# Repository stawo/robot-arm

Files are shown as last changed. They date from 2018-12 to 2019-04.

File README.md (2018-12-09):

This is a small project aimed at building a 6 DOF robot arm using inexpensive components, and control it through a Raspberry Pi.

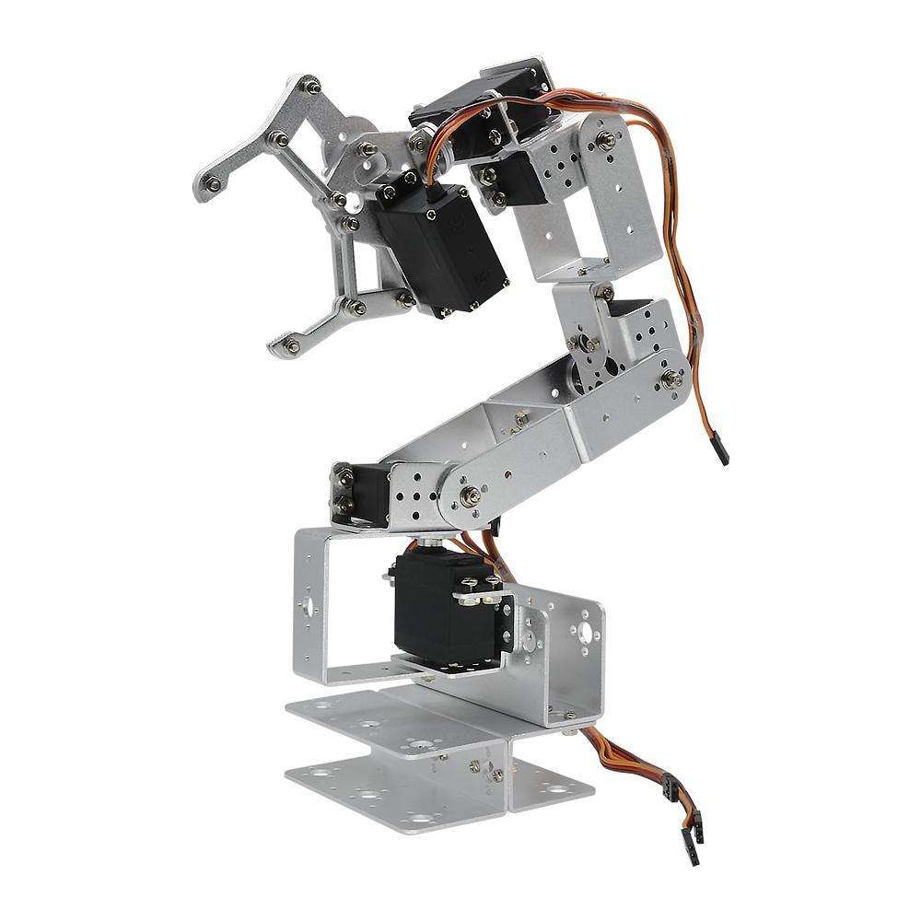
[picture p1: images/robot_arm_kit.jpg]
robot arm kit Robot Arm Kit


# Table of Contents
- [Table of Contents](#table-of-contents)
- [BOM](#bom)
- [Some Theory](#some-theory)
  - [Controlling Servo Motors](#controlling-servo-motors)
  - [Servo motor feedback](#servo-motor-feedback)
- [Raspberry Pi configuration](#raspberry-pi-configuration)
  - [Raspberry Pi set up](#raspberry-pi-set-up)
  - [Controlling servo motors with Raspberry Pi and the PWM Driver PCA9685](#controlling-servo-motors-with-raspberry-pi-and-the-pwm-driver-pca9685)
  - [Reading the feedback from servo motors with Raspberry Pi](#reading-the-feedback-from-servo-motors-with-raspberry-pi)

# BOM
List of components used:
* Raspberry Pi 2 Model B
* 32GB Micro SD card
* Robot Arm mechanical kit (Diymore ROT3U 6DOF Aluminium Robot Arm Mechanical Clamp Claw Kit, https://www.amazon.de/gp/product/B01LY4RHX2/)
* 6x Servo Motors (Lewan Soul LD-27MG, http://www.lewansoul.com/product/detail-19.html)
* 12V 30A Switching Power Supply (Xktts Ueercrr 12V 30A 360W, https://www.amazon.de/gp/product/B00P2CTT26)
* DC/DC 4.5-30V to 1-30V 12A Buck Converter (https://www.amazon.de/gp/product/B00HV4EPG8)
* Dual USB DC/DC Step Down Converter (https://www.amazon.de/gp/product/B0768D2NYH)
* Sunfounder PCA9685 16 Channel 12 Bit PMW Servo Driver (http://wiki.sunfounder.cc/index.php?title=PCA9685_16_Channel_12_Bit_PWM_Servo_Driver)
* 4x 45 cm Servo Extension Cable (https://www.amazon.de/gp/product/B01M7N77XC)
* 4x 20cm female-female Dupont jumper wire cable (https://www.amazon.de/gp/product/B00OL6JZ3C)
* 3-cores electric wire with plug
* 2-cores wire
* screws/nails
* USB-Micro USB cable

Tools:
* Multimeter
* Electric screwdriver
* Monitor/Keyboard/Mouse/Wi-Fi adapter/SD Adapter for Micro SD for the Raspberry Pi

Just to give a reference, I personally ordered almost everything on Amazon for the sake of simplicity (or laziness), and spent around 200€.

|**NOTE**|
|--------|
|The servo motors have to be physically modified in order to read the internal potentiometer.|

# Some Theory
Before moving on, it is necessary to understand how the various elements work, especially parts like servo motors, in order to avoid problems (i.e., avoid burning stuff like me due to too much excitement and not knowing how things work!).

## Controlling Servo Motors
A servo motor is usually controllable through PWM (Pulse Width Modulation). Specifically, its arm position depends on the width (or length) of the pulse applied to it.
A PWM signal encodes a ratio. The ratio of on to off is needed to get all the information; on alone is not enough. 
As a concrete example, PWM might be running at a frequency of 200Hz (or a period of 5ms). A 50% of maximum power signal (also known as Duty Cycle) would be on for 2.5ms, and off for 2.5ms. 
Change the frequency to 1000Hz, and hence the period becomes 1ms. The 50% duty cycle would now be 0.5ms on, and 0.5ms off. That PWM signal still encodes the same 50% power information.

Usually, servos can rotate between 0 and 180°. So we have to adjust the pulse length in between. A length of 1.5ms (7.5% duty cycle) thus gives an angle of 90°. And all at precisely 50 times per second (50Hz).
This diagram summarizes how a servo motor is controlled through PWM:

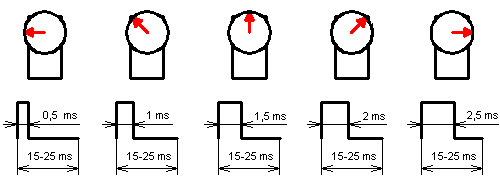
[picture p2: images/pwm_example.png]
pwm example PWM Example


In my case I use the Lewan Soul LD-27MG, which has the following specs:
* working voltage: 6-7.4 V
* min working current: 1 A
* angle: between 0° and 270°
* Pulse Period: 20ms
  thus Frequency: 50Hz
* Pulse Width Range: between 0.5ms and 2.5ms
  thus Duty Cycle: between 2.5% and 12.5%

Conversion table:
Angle   | Pulse Width (ms) | Duty Cycle (%)
------- | ---------------- | --------------
0°      | 0.5              | 2.5
45°     | 0.8333           | 4.1666
90°     | 1.1666           | 5.8333
135°    | 1.5              | 7.5
180°    | 1.8333           | 9.1666
225°    | 2.1666           | 10.8333
270°    | 2.5              | 12.5

Links:
* https://www.teachmemicro.com/raspberry-pi-pwm-servo-tutorial/
* https://tutorials-raspberrypi.com/raspberry-pi-servo-motor-control/

## Servo motor feedback
Normal servo motors do not provide a feedback to the control board (in our case, the Raspberry Pi).
They simply take the PWM generated and do their best to fulfill the "request".

For our robot arm this is not ideal, because the arm could get stuck while doing a movement (for example, we try to push the arm against the table), and this leads to a stall of the servo motor.
Stalling a servo motor will damage it and the control board, as it will increase the current load (see https://electronics.stackexchange.com/questions/274721/how-does-blocking-a-servo-dc-motor-break-it).

Especially in my setup, once the PCA9685 control board sends the PWM signal to the servo motor, there is no way to stop the PWM signal or turn off the servo, and the board will burn out (it happened to me) if the servo stalls.

To understand if a servo motor is in stall (or, alternatively, is operating correctly), we need a feedback from it.
We can achieve this by tapping the potentiometer inside the servo motor, and read the measured voltage.

**[TO DO: How to modify the servo motors]**

Links:
* https://www.youtube.com/watch?v=w7qRs6tvxlM
* https://learn.adafruit.com/analog-feedback-servos/using-feedback
* https://electronics.stackexchange.com/questions/214761/how-to-measure-servo-potentiometer

# Raspberry Pi configuration

I'm running the Raspberry Pi using Raspbian Stretch with desktop (https://www.raspberrypi.org/downloads/raspbian/).

Here is the Raspberry Pi GPIO layout (http://pi4j.com/pins/model-2b-rev1.html) for reference:
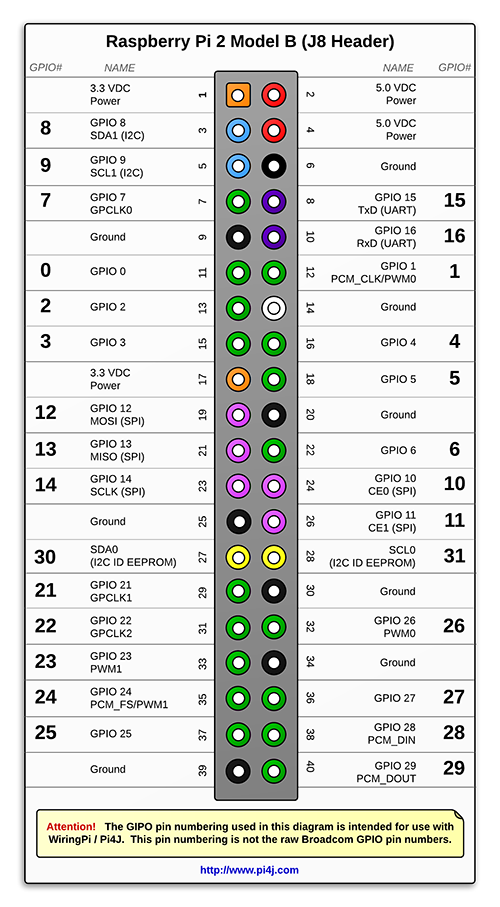
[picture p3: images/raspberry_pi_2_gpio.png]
raspberry pi gpio Raspberry Pi 2 GPIO


## Raspberry Pi set up
To be able to control servo motor through the PCA9685 controller, we need to perform the following steps:
1. Activate the I2C interface in the Raspberry
    * run the command
    ``sudo raspi-config``
    * go to “Interfaces”, select “I2C”, select “Yes”
2. Configuring Raspberry Pi for I2C.
    * Install the following packages:
    ``sudo apt-get install python-smbus``
    ``sudo apt-get install i2c-tools``
    * Add the following lines to ``/etc/modules``:
    ``i2c-dev``
    ``i2c-bcm2708``
    * Reboot the Pi
3. Check that the PCA9685 controller is properly connected and it's set to its default address:
  ``sudo i2cdetect -y 1``
  It should show up at 0x40 (binary 1000000) as follows:
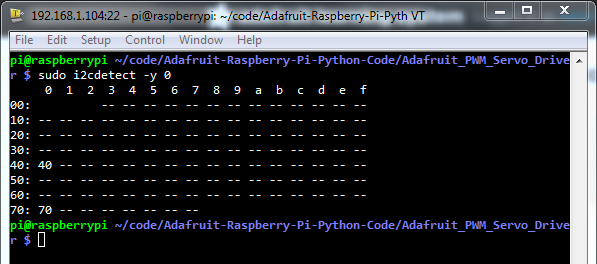
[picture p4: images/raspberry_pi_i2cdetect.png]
raspberry pi i2cdetect i2cdetect
  
4. Connect the PCA9685 controller as in the diagram
5. [optional] Create/activate the Python environment of your choice
6. Install the library https://github.com/adafruit/Adafruit_Python_PCA9685 by running the command:
  ``sudo pip install adafruit-pca9685``

Links:
* https://learn.adafruit.com/adafruit-16-channel-servo-driver-with-raspberry-pi/configuring-your-pi-for-i2c

## Controlling servo motors with Raspberry Pi and the PWM Driver PCA9685
**[TO DO]**

## Reading the feedback from servo motors with Raspberry Pi
**[TO DO]**

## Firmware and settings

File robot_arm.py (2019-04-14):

# ----------------------------
# LIBRARIES

# External libraries
import time
# Import the PCA9685 module.
import Adafruit_PCA9685
import board
import busio
import adafruit_ads1x15.ads1115 as ADS
from adafruit_ads1x15.analog_in import AnalogIn
import pandas

# Uncomment to enable debug output.
#import logging
#logging.basicConfig(level=logging.DEBUG)

# ----------------------------
# PARAMETERS

# ----------------------------
# CODE

class Servo:

    # PARAMETERS
    SERVO_MOTOR_DUTY_CYCLE_MIN = 2.5  # Min duty cycle, in %
    SERVO_MOTOR_DUTY_CYCLE_MAX = 12.5  # Max duty cycle, in %
    SERVO_MOTOR_ANGLE_MIN = 0  # Min angle, in degrees
    SERVO_MOTOR_ANGLE_MAX = 270  # Max angle, in degrees
    
    # Angle to cover at each step of the calibration
    # We define it so we can have clear ads values between each step,
    # as the ads readings fluctuate, and too close angles will not be
    # easily distinguishable.
    SERVO_MOTOR_ANGLE_CALIBRATION_STEP = 10

    # We define how many seconds the feedback loop will
    # wait while the servo tries to reach the designated angle
    # before intervening if no movement is detected.
    # This is needed in those situations where the servo is
    # blocked but keeps trying to reach the desired angle.
    MAX_TIME_BEFORE_EMERGENCY_STOP = 1

    # Value for the alpha parameter in the calculation of
    # the exponential moving average (ema)
    # https://en.wikipedia.org/wiki/Moving_average#Exponential_moving_average
    CALIBRATION_EMA_ALPHA = 0.8
    # Percentage that says when the ema converged to a
    # value that can be considered stable
    CALIBRATION_EMA_CONVERGENCE_PERCENTAGE = 0.001
    # CALIBRATION_EMA_CONVERGENCE_ABSOLUTE = 0.001

    def __init__(
        self
        , pwm_board
        , pwm_board_servo_channel
        , pwm_board_resolution
        , angle_min
        , angle_max
        , ads_board
        , ads_board_channel
        , angle_ads_value_map):
        
        if not isinstance(pwm_board, Adafruit_PCA9685.PCA9685):
            raise ValueError('The pwm_board parameter must be a Adafruit_PCA9685.PCA9685 instance.')
        
        if not isinstance(pwm_board_servo_channel, int) and pwm_board_servo_channel >= 0:
            raise ValueError('The pwm_board_servo_channel parameter must be a positive integer >= 0.')
        
        if not isinstance(pwm_board_resolution, int) and pwm_board_resolution > 0:
            raise ValueError('The pwm_board_resolution parameter must be a positive integer > 0.')
        
        if not isinstance(ads_board, ADS.ADS1115):
            raise ValueError('The ads_board parameter must be a ADS.ADS1115 instance.')
        
        if not isinstance(ads_board_channel, int) and ads_board_channel >= 0:
            raise ValueError('The ads_board_channel parameter must be a positive integer >= 0.')
        
        self.PWM_BOARD = pwm_board
        self.PWM_BOARD_SERVO_CHANNEL = pwm_board_servo_channel
        self.PWM_BOARD_RESOLUTION = pwm_board_resolution
        self.ADS_BOARD = ads_board
        self.ADS_BOARD_CHANNEL = ads_board_channel
        
        # If the Servo motor doesn't have a valid angle_ads_value_map
        # we do not allow it to move
        self.BLOCKED = True

        self.__ads_chan = AnalogIn(self.ADS_BOARD, self.ADS_BOARD_CHANNEL)

        if isinstance(angle_ads_value_map, pandas.DataFrame) \
            and angle_ads_value_map.columns.values.tolist() == ['angle','ads_value']:
            self.BLOCKED = False
            self.ANGLE_ADS_VALUE_MAP = angle_ads_value_map

            # Try to evaluate the current position of the servo
            self.current_angle = self.__evaluate_current_angle()
    
    def __evaluate_current_angle(self):
        """
        Function to evaluate the current angle based on the ads value.

        To evaluate the current angle of the servo we:
        * read the current ads value
        * use the angle_ads_value_map to estimate the angle

        Returns
		-------
            int
            The estimated angle of the servo.

        """

        current_ads_value = self.__ads_chan.value
        closest_angle = self.ANGLE_ADS_VALUE_MAP.ix[(self.ANGLE_ADS_VALUE_MAP.ads_value-current_ads_value).abs().argsort()[:1]].angle.values[0]
        
        return closest_angle
        
    def __convert_angle_to_pwm_board_step(self, angle):
        '''
        Transform a given angle to the proper step for the PWB board.
        Usually boards like the PCA9685 uses a discrete representation for the PWM.
        They divide the Pulse Cycle in 4096 steps, and we have to say from
        which step to which step we want the pulse to be high.

        We assume that, for servo motors, the first step is 0,
        so we just have to calculate the ending step, so to represent the given angle
        as a discrete PWM.

        To calculate the step, we first calculate the relative duty cycle of the angle.
        We then multiply the PWM_BOARD_RESOLUTION by the duty cycle (which is a percentage).
        '''
        
        # Round the angle to the closest valid one w.r.t. SERVO_MOTOR_ANGLE_CALIBRATION_STEP
        angle = int(angle) - int(angle)%self.SERVO_MOTOR_ANGLE_CALIBRATION_STEP
         
        # Check that the angle is within the limits
        if (angle < self.SERVO_MOTOR_ANGLE_MIN) | (angle > self.SERVO_MOTOR_ANGLE_MAX):
            raise ValueError('The given angle ({}) is outside the limits!'.format(angle))

        # We make sure angle is treated as a float
        servo_duty_cycle = float(angle)/(self.SERVO_MOTOR_ANGLE_MAX-self.SERVO_MOTOR_ANGLE_MIN)*(self.SERVO_MOTOR_DUTY_CYCLE_MAX-self.SERVO_MOTOR_DUTY_CYCLE_MIN) + self.SERVO_MOTOR_DUTY_CYCLE_MIN

        # Check that the duty cycle is within the limits
        # This check is just to be sure that also the angle parameters are set correctly
        if (servo_duty_cycle < self.SERVO_MOTOR_DUTY_CYCLE_MIN) | (servo_duty_cycle > self.SERVO_MOTOR_DUTY_CYCLE_MAX):
            raise ValueError('The given servo duty cycle ({}) is outside the limits!'.format(servo_duty_cycle))

        # The step must be an integer, as the board does not accept floats
        pwm_step = int(self.PWM_BOARD_RESOLUTION*servo_duty_cycle/100)

        # print('angle: {}\tservo_duty_cycle: {}\tpwm_step: {}'.format(angle,servo_duty_cycle,pwm_step))

        return pwm_step

    def __move(self, angle, raise_if_out_of_range = False):
        '''
        Function that moves the specified servo to the given angle.
        It has no feedback control!

        We use this function as the low-level instruction to move
        the servo used by other functions of the class if needed.
        '''

        if raise_if_out_of_range:
            if angle < self.SERVO_MOTOR_ANGLE_MIN: raise ValueError('The given angle ({}) is outside the limits!'.format(angle))
            if angle > self.SERVO_MOTOR_ANGLE_MAX: raise ValueError('The given angle ({}) is outside the limits!'.format(angle))
        else:
            # If the specified angle is out of range, we block it to the closest limit
            if angle < self.SERVO_MOTOR_ANGLE_MIN: angle = self.SERVO_MOTOR_ANGLE_MIN
            if angle > self.SERVO_MOTOR_ANGLE_MAX: angle = self.SERVO_MOTOR_ANGLE_MAX
        
        pwm_step = self.__convert_angle_to_pwm_board_step(angle)
        self.PWM_BOARD.set_pwm(self.PWM_BOARD_SERVO_CHANNEL, 0, pwm_step)

    def calibrate(self, calibration_map_path):
        
        print('CALIBRATION OF THE SERVO MOTOR')
        print('This function will move the servo motor from {} (SERVO_MOTOR_ANGLE_MIN) to {} (SERVO_MOTOR_ANGLE_MAX),'.format(self.SERVO_MOTOR_ANGLE_MIN,self.SERVO_MOTOR_ANGLE_MAX))
        print('and register the output value of the ADS board.')
        print()
        print('MAKE SURE THE SERVO IS FREE TO MOVE!')
        answer = input("Enter YES to proceed: ")
        if answer.lower() != "yes":
            print("I will not continue the calibration.")
            return

        print('Starting calibration.')

        calibration_map_angle_to_ads_value = []

        # Move to the minimum angle, in case the servo is at another angle
        self.__move(self.SERVO_MOTOR_ANGLE_MIN)

        # Initialize the exponential moving average        
        ema = self.__ads_chan.value
        
        TIME_STEP_DURATION = 0.2
        NUM_OF_TIME_STEPS = 10

        # We let the ems to be estimated over some cycles
        # before checking if it converged
        for counter in range(NUM_OF_TIME_STEPS):
            old_ema = ema
            ema = self.CALIBRATION_EMA_ALPHA*self.__ads_chan.value + (1-self.CALIBRATION_EMA_ALPHA)*ema
            
            print('value: {:.2f}\t\tema: {:.2f}\t\tdiff percentage: {:.4f}'.format(self.__ads_chan.value,ema,abs((ema-old_ema)/ema)))
            
            time.sleep(TIME_STEP_DURATION)
        
        while True:
            old_ema = ema
            ema = self.CALIBRATION_EMA_ALPHA*self.__ads_chan.value + (1-self.CALIBRATION_EMA_ALPHA)*ema
            
            print('value: {:.2f}\t\tema: {:.2f}\t\tdiff percentage: {:.4f}'.format(self.__ads_chan.value,ema,abs((ema-old_ema)/ema)))
            
            if abs((ema-old_ema)/ema) <= self.CALIBRATION_EMA_CONVERGENCE_PERCENTAGE: break
            
            time.sleep(TIME_STEP_DURATION)
            
        
        print('Moved to 0.')
        time.sleep(2)

        # Move to the minimum angle, in case the servo is at another angle
        # self.__move(self.SERVO_MOTOR_ANGLE_MIN)
        # print('Moved to 0.')
        # time.sleep(2)
        
        for angle in range(self.SERVO_MOTOR_ANGLE_MIN,self.SERVO_MOTOR_ANGLE_MAX+1, self.SERVO_MOTOR_ANGLE_CALIBRATION_STEP):
            
            self.__move(angle)

            # Initialize the exponential moving average
            ema = self.__ads_chan.value

            # We let the ems to be estimated over some cycles
            # before checking if it converged
            for counter in range(NUM_OF_TIME_STEPS):
                old_ema = ema
                ema = self.CALIBRATION_EMA_ALPHA*self.__ads_chan.value + (1-self.CALIBRATION_EMA_ALPHA)*ema
                
                print('value: {:.2f}\t\tema: {:.2f}\t\tdiff percentage: {:.4f}'.format(self.__ads_chan.value,ema,abs((ema-old_ema)/ema)))
                
                time.sleep(TIME_STEP_DURATION)
            
            while True:
                old_ema = ema
                ema = self.CALIBRATION_EMA_ALPHA*self.__ads_chan.value + (1-self.CALIBRATION_EMA_ALPHA)*ema
                
                print('value: {:.2f}\t\tema: {:.2f}\t\tdiff percentage: {:.4f}'.format(self.__ads_chan.value,ema,abs((ema-old_ema)/ema)))
                
                if abs((ema-old_ema)/ema) <= self.CALIBRATION_EMA_CONVERGENCE_PERCENTAGE: break
                
                time.sleep(TIME_STEP_DURATION)
            
            
            self.current_angle = angle

            # Read voltage and use it to evaluate if the servo is stuck
            calibration_map_angle_to_ads_value.append([angle,self.__ads_chan.value])

            print('Moved to angle {}, ads value is {}'.format(angle,self.__ads_chan.value))
        
        calibration_map_angle_to_ads_value_df = pandas.DataFrame(calibration_map_angle_to_ads_value, columns = ['angle','ads_value'])
        calibration_map_angle_to_ads_value_df.to_csv(calibration_map_path, index=False)

    def move(self, angle):
        '''
        We move the specified servo to the given angle.
        We check the ads value for feedback and use it
        to either continuing the movement or block it.

        The process is as follow:
        - divide the desired angle in steps
        - for each step:
            - move to the current step
            - check every X seconds if the servo actually moved
            by reading the ads value
            - if no movement is detected, try to move back to the
            last step

        '''

        if self.BLOCKED:
            raise ValueError('The Servo motor is blocked. Cannot perform movements!')

        print('Move to angle {}'.format(angle))

        starting_angle = self.current_angle
        versus = 'UP' if angle > starting_angle else 'DOWN'

        for partial_angle in range(starting_angle, angle, self.SERVO_MOTOR_ANGLE_CALIBRATION_STEP):
            
            self.__move(partial_angle)
            
            start_time = time.time()

            while True:
                time.sleep(0.2)
                
                evaluated_angle = self.__evaluate_current_angle()

                if (time.time()-start_time) >= MAX_TIME_BEFORE_EMERGENCY_STOP:
                    
                    if (versus == 'UP' and self.current_angle <= evaluated_angle):
                        pass

            
            self.current_angle = partial_angle

class RobotArm:

    # PARAMETERS
    PWM_BOARD_RESOLUTION = 4096 # PWM control board resolution
    SERVO_MOTOR_FREQUENCY = 50 #In Hz
    
    JOINT_0_ANGLE_ADS_VALUE_MAP_PATH = 'data/angle_ads_value_map_joint_0.csv'

    def __init__(self):
        
        print('Initialize PWM board controller')
        # Initialise the PCA9685 using the default address (0x40).
        self.__pwm = Adafruit_PCA9685.PCA9685()

        print('Set frequency')
        # Set the frequency
        self.__pwm.set_pwm_freq(self.SERVO_MOTOR_FREQUENCY)

        self.__i2c = busio.I2C(board.SCL, board.SDA)
        self.__ads1 = ADS.ADS1115(self.__i2c)
        # self.__ads2 = ADS.ADS1115(i2c)
        
        self.__joints = []
        self.__joints.append(Servo(self.__pwm,0,self.PWM_BOARD_RESOLUTION,0,270,self.__ads1,0, pandas.read_csv(self.JOINT_0_ANGLE_ADS_VALUE_MAP_PATH)))
        # self.__joints.append(Servo(self.__pwm,1,self.PWM_BOARD_RESOLUTION,0,270,self.__ads1,1))
        # self.__joints.append(Servo(self.__pwm,2,self.PWM_BOARD_RESOLUTION,0,270,self.__ads1,2))
        # self.__joints.append(Servo(self.__pwm,3,self.PWM_BOARD_RESOLUTION,0,270,self.__ads1,3))
        # self.__joints.append(Servo(self.__pwm,4,self.PWM_BOARD_RESOLUTION,0,270,self.__ads2,0))
        # self.__joints.append(Servo(self.__pwm,5,self.PWM_BOARD_RESOLUTION,0,270,self.__ads2,1))

    def move(self):
        
        print('Move the servo')
        self.__joints[0].move(0)
        # self.__joints[1].move(0)
        time.sleep(3)
        
        self.__joints[0].move(180)
        # self.__joints[1].move(90)
        time.sleep(3)
        
        self.__joints[0].move(90)
        # self.__joints[1].move(270)
        time.sleep(3)
        
        self.__joints[0].move(120)
        # self.__joints[1].move(200)
        time.sleep(3)

def calibrate_servos():
    
    PWM_BOARD_RESOLUTION = 4096 # PWM control board resolution
    SERVO_MOTOR_FREQUENCY = 50 #In Hz
    JOINT_0_ANGLE_ADS_VALUE_MAP_PATH = 'data/angle_ads_value_map_joint_0.csv'

    print('Initialize PWM board controller')
    # Initialise the PCA9685 using the default address (0x40).
    pwm = Adafruit_PCA9685.PCA9685()

    print('Set frequency')
    # Set the frequency
    pwm.set_pwm_freq(SERVO_MOTOR_FREQUENCY)

    i2c = busio.I2C(board.SCL, board.SDA)
    ads1 = ADS.ADS1115(i2c)

    servo0 = Servo(pwm,0,PWM_BOARD_RESOLUTION,0,270,ads1,0, None)

    servo0.calibrate(JOINT_0_ANGLE_ADS_VALUE_MAP_PATH)

if __name__ == "__main__":
    
    # robot_arm = RobotArm()
    # robot_arm.move()

    calibrate_servos()

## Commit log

2018-12-09 Initial documentation for the project.
    [RaspberryPi-PCA9685-Servo Connection.fzz]
2018-12-09 Test program to move a servo motor.
2018-12-09 Fixed function for waiting time.
    [test.py]
2018-12-09 Initial script for controlling the robot arm.
2018-12-09 Added a second servo for testing.
2018-12-10 Added manual control of servo for testing.
2019-04-14 Added calibration for servo, rewritten move func.
